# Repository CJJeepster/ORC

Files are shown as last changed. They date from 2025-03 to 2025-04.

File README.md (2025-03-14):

# ORC
WSU Capstone 2025

ORC is a active suspension system for an RC car, in this case RC4WD's Trail finder 2. The design documentation, source code, python code, custom parts, schematics, and PCBs are included in their own folders. 

The source code is intended to be built with Espressif's ESP-ID v5.4.0, which can be a standalone toolchain, or VScode extension. 
The python code is run with python 3.12 using the following libraries: csv, matplotlib, numpy, scipy, and collections. This will take the logged data, calculate some statistics, and plot the repeated runs.
The custom parts were designed in FreeCAD 1.0.0, with both STL files and the original files included. 
The schematics and PCBs were designed in KiCAD 8.0. A seperate "revisions" document details the shortcomings of this design. Fixes are not yet implemented to preserve the current state of the board and save development time.

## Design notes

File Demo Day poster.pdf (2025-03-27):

Corbin Roennebeck
Department of Electrical and Computer Engineering Weber State University

## Introduction

## Project Goals

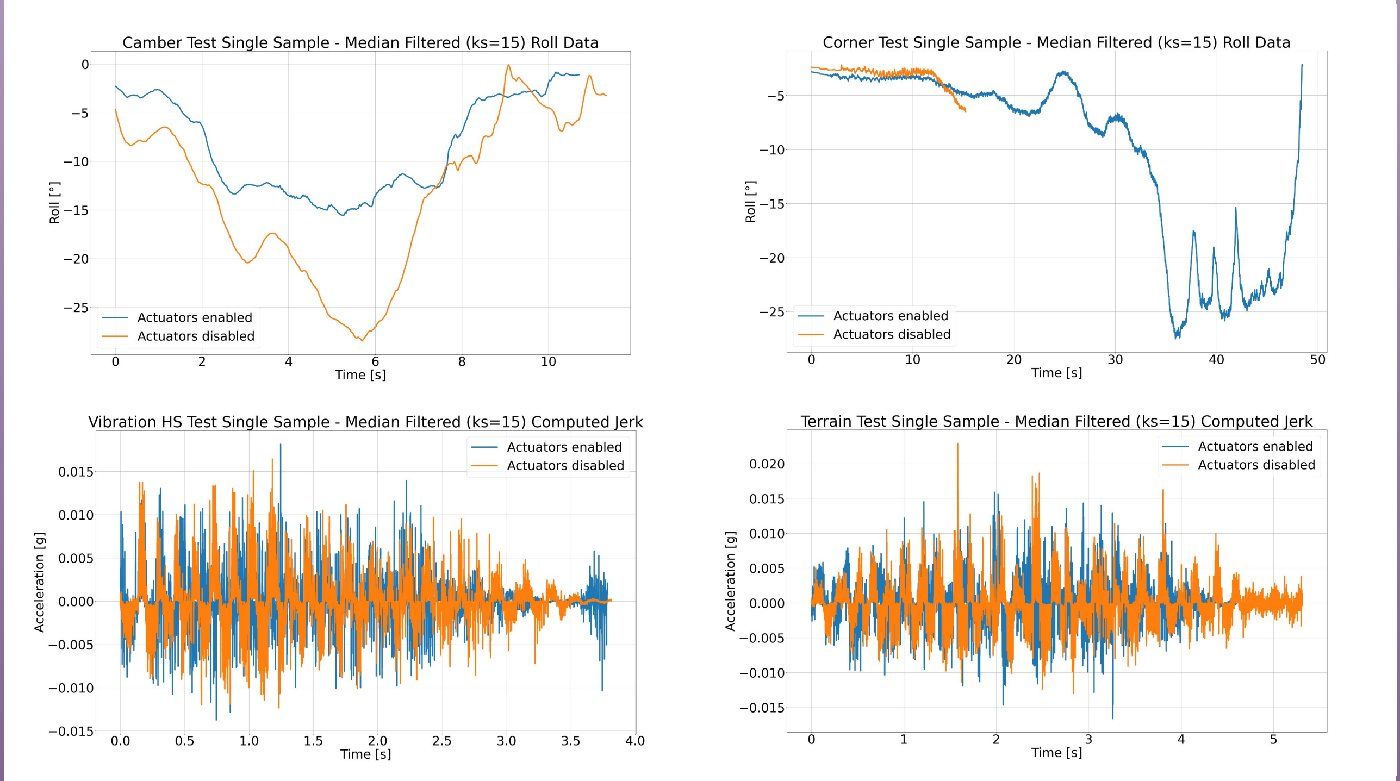
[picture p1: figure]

## Methods

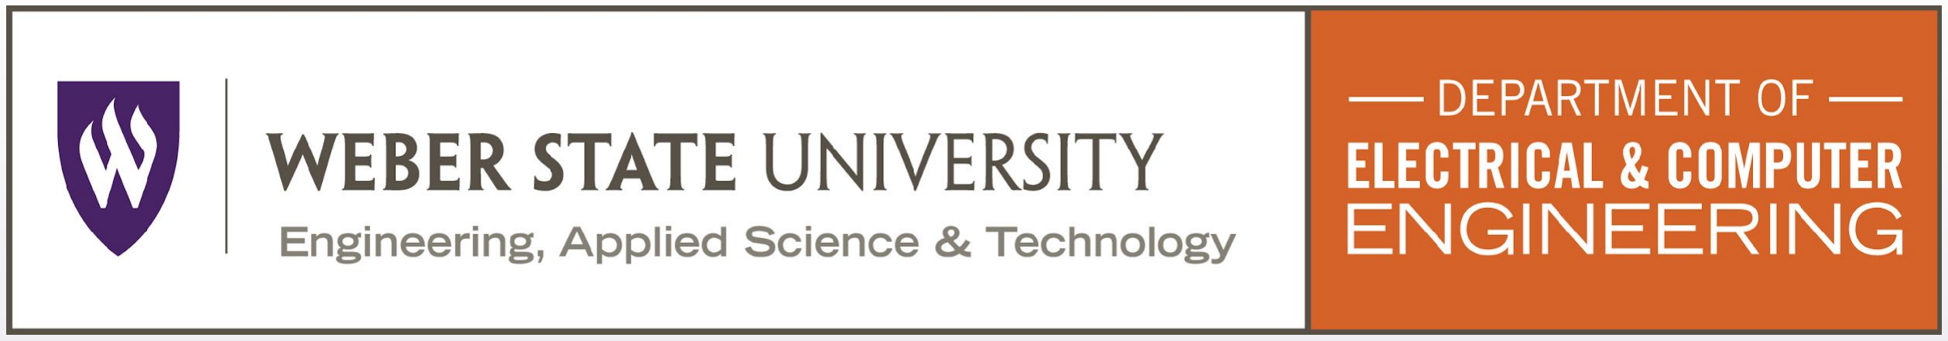
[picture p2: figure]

Figures and Results | Conclusion

## Acknowledgments

## References

The Off-Road Roll Control (ORC) project seeks to provide high performance vehicle suspension at budget build prices. Large off road vehicles, like the modern Jeep Wrangler, are top heavy and prone to rolling over in off-balance situations. This problem is exacerbated by disconnected sway bars, lifted suspensions, roll cages, and body armor.
In extreme cases, a vehicle similar to the one described prior could roll over as a result of a low speed emergency maneuver. To help mitigate handling issues like this and to improve passenger comfort overall, an active suspension system is proposed here.

Similar to [1], PID control of actuators is the primary control methodology. The PID controllers respond to vertical acceleration, pitch, and roll. These are measured by an inertial measurement system (IMU), the data from which is combined and filtered. The output of the 3 PIDs are transformed into 4 actuator movements, present at each corner of the vehicle. The outer loop from [1] is excluded as its effect was minimal and increased complexity significantly. Were development of this platform to continue, better tuning, or automatic tuning, of the PID controllers could reveal more performance. Other control algorithms such as fuzzy logic or the many others suggested in [3] could be tested. Using a voice coil actuator could also prove to improve ride quality further by decreasing response time.

# Off-Road Roll Control

Many thanks are extended to the ECE department faculty, especially Dr. Fon Brown, for their extensive support and excellent guidance.
Special thanks are due to Audrey Roennebeck, without whose support this project would not have been possible.

To implement actuators on a scale prototype, several solutions were explored, but ultimately a gear motor with a lever arm was chosen. This solution allowed the suspension to move freely, without too much damping coming from the motors themselves. These gear motors are mounted to the frame of an 1/10 scale RC rock crawler. Linkages connect the lever arm to the axle on both the driver and passenger side of the vehicles. By varying the magnitude and polarity of the current sent to these motors, a variable force between the axle and frame can be realized.
This variable current comes from the custom motor driver boards, which take a ±2.5V signal from the main board’s DAC and converts it to a ±16V signal used to drive the motors up to about 2A.

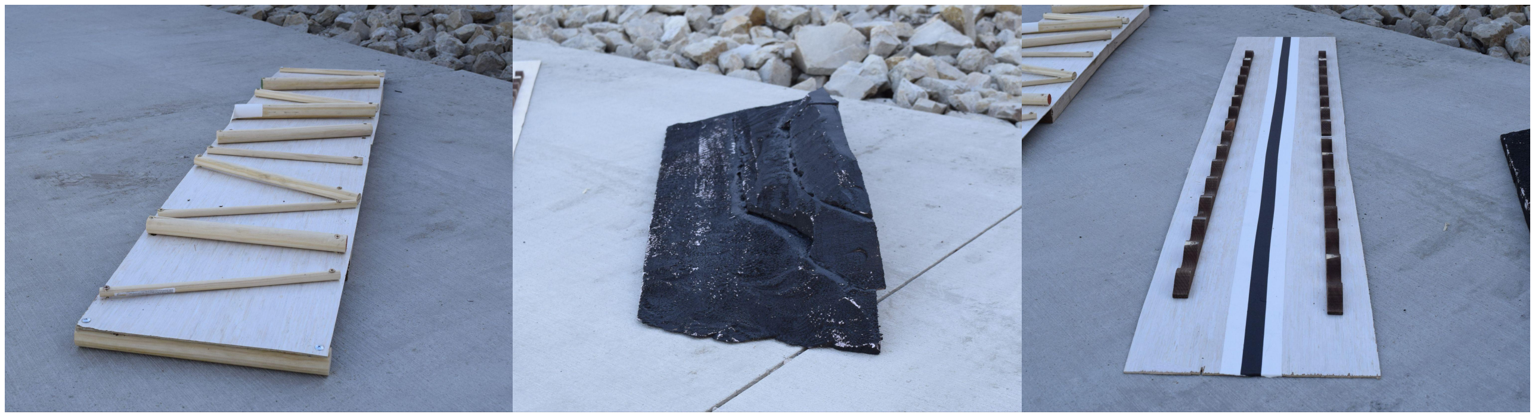
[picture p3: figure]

[1] D. Tan, C. Lu, and X. Zhang, “Dual-loop PID control with PSO algorithm for the active suspension of the electric vehicle driven by in-wheel motor,” Journal of Vibroengineering, vol. 18, no. 6, pp. 3915–3929, Sep. 2016, doi: 10.21595/jve.2016.16689.
[2] J. Sun, J. Cong, W. Zhao, and Y. Zhang, “Quantized Feedback Control of Active Suspension Systems Based on Event Trigger,” Shock and vibration, vol. 2021, pp. 1–15, May 2021, doi: https://doi.org/10.1155/2021/8886069.
[3] Kevin Herubiel Floreán-Aquino, M. Arias-Montiel, J. Linares-Flores, José Gabriel Mendoza-Larios, and
A. Cabrera-Amado, “Modern Semi-Active Control Schemes for a Suspension with MR Actuator for Vibration Attenuation,” Actuators, vol. 10, no. 2, pp. 22–22, Jan. 2021, doi: https://doi.org/10.3390/act10020022.

ORC improves passenger comfort by reducing experienced pitch, roll, and vertical jerk relative to a vehicle with no dampers. A real time system contained to only the equipped vehicle is desired. For practical reasons, a 1/10 scale vehicle platform is demonstrated.

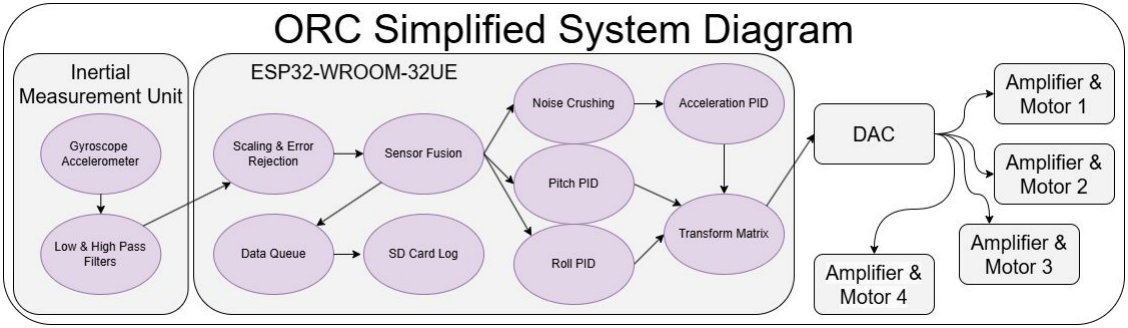
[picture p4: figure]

To examine the effects of the control system on vehicle dynamics, the pitch, roll, and vertical acceleration of the vehicle are recorded. From the vertical acceleration data, the jerk (representing the smoothness of the ride) can be derived. This data is recorded while driving over bumpy terrain, off camber, and through tight corners.
The same terrain (pictured below) is used for testing with actuators enabled, and disabled. Each terrain is driven with a constant speed and minor steering inputs to keep the vehicle on track. Where possible, 20+ test runs were conducted for each actuator status.

One Sided T Test Statistics For Improved (Absolutely Less) RMS, Minimum, and Maximum Values

P-value\Test | Camber (min direction) | Terrain | Vibration High Speed* | Vibration Low Speed | Corner*
Acceleration RMS | 6.27E-20 | 3.84E-03 | 1.06E-06 | 1.10E-09 | 1.00E+00
Pitch RMS | 1.19E-07 | 1.65E-09 | 1.65E-01 | 3.10E-33 | 9.92E-01
Roll RMS | 9.81E-20 | 2.92E-27 | 1.54E-02 | 1.02E-24 | 9.22E-01
Jerk RMS | 1.00E+00 | 1.00E+00 | 4.45E-01 | 1.00E+00 | 9.89E-01
Acceleration MIN | 7.92E-14 | 9.44E-01 | 4.42E-05 | 1.00E+00 | 7.28E-01
Pitch MIN | 6.98E-13 | 1.15E-05 | 1.78E-01 | 4.59E-01 | 9.69E-01
Roll MIN | 2.93E-35 | 4.83E-21 | 3.16E-04 | 5.79E-26 | 9.65E-01
Jerk MIN | 1.00E+00 | 1.00E+00 | 9.96E-01 | 1.00E+00 | 8.33E-01
Acceleration MAX | 9.97E-01 | 4.26E-01 | 1.52E-06 | 1.38E-18 | 9.89E-01
Pitch MAX | 1.00E+00 | 3.26E-16 | 9.15E-03 | 2.53E-27 | 9.83E-01
Roll MAX | 6.18E-01 | 7.81E-34 | 3.91E-04 | 2.40E-12 | 8.60E-01
Jerk MAX | 1.00E+00 | 9.08E-03 | 7.33E-01 | 1.00E+00 | 8.30E-01

*Only tested 5 samples instead of full 20+
(Gray fill not relevant to particular test, included for completeness) | >5% CI | <5% CI

The ORC system’s ability to reduce vehicle roll and jerk is mixed. In almost every case the roll of the vehicle was statistically significantly reduced. In all but one case the experienced jerk was not shown to be significantly less when the actuators were enabled. This is not to say the vehicle performed worse, but the difference between the groups was not large enough to be decisive.
A two sample one sided t-test was used to show statistically significant improvement in ride quality within a 5% confidence interval (CI). The RMS, minimum, and maximum value of each test run was put in one of two data sets (actuators enabled/disabled). This does assume the data follows a normal distribution.
While not part of the initial testing plan, the number of revolutions completed in the corner test was evaluated. This showed significant improvement in cornering ability with a P value of 0.0166, which is well within the 5% CI.
Overall, ORC was successful in improving ride quality, but it is likely that some performance was still left on the table.

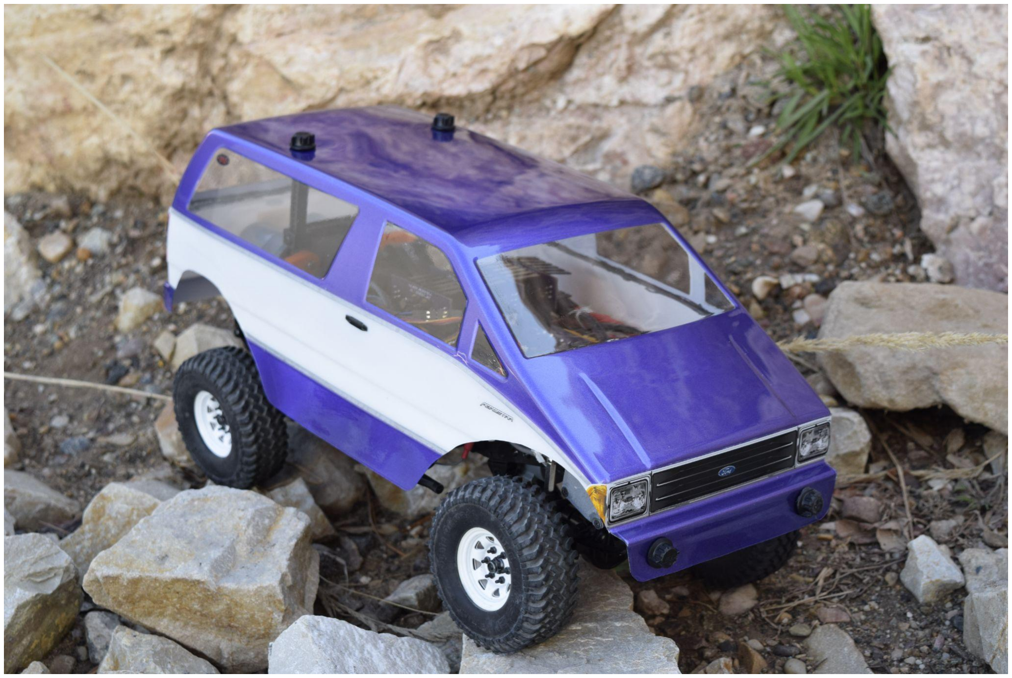
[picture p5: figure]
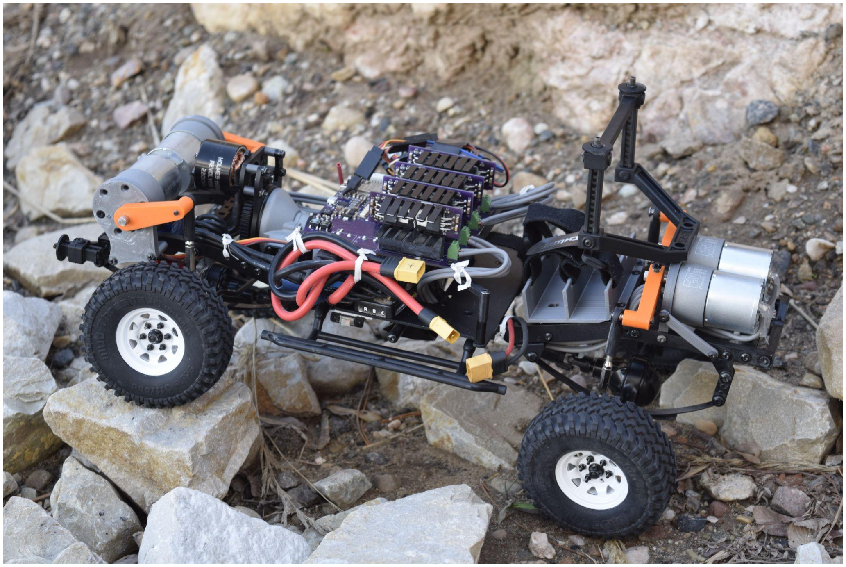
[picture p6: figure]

The collected data was processed with a Python script that applied a median filter to knock out random peak readings, plotted a single run’s data, and performed a one-sided T-test, discussed in the next section. Selected plots are displayed below.

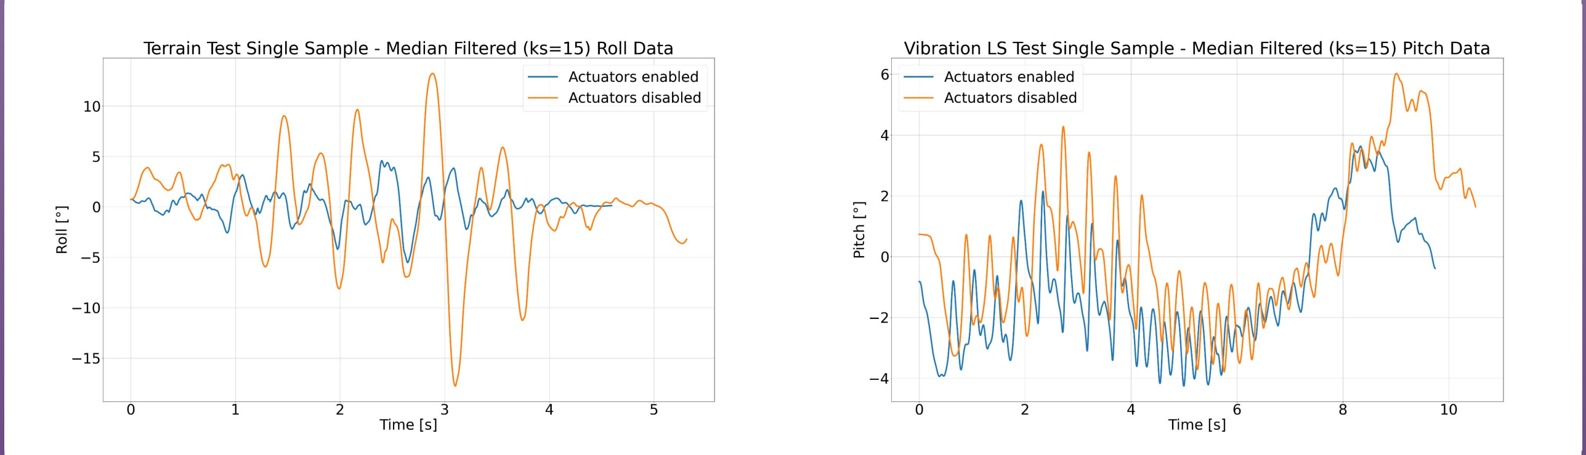
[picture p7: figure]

All of the plots and test results are fairly representative of the actual vehicle dynamics except those from the corner test. This test involved driving at increasing speed with a fixed steering input until the vehicles max speed was reached or the vehicle rolled. The induced centrifugal force confused the sensor fusion algorithm, causing it to misinterpret the direction of gravity and thus the euler angles of the system. To combat this, the number of revolutions completed by the vehicle were counted, where the vehicle with the actuators enabled completed 30.9 rotations on average compared to the actuators disabled completing an average of 5.5.

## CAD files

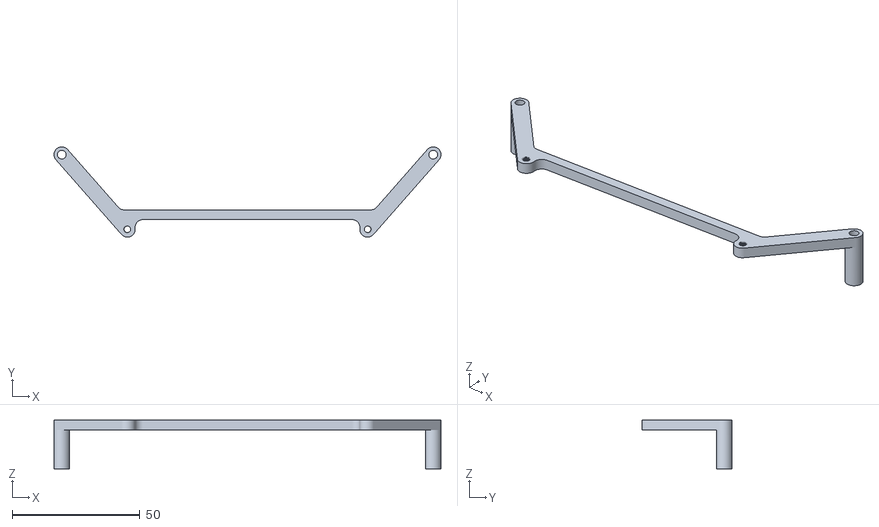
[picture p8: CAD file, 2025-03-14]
3D models/stl/main board mount rear-BodyMirrored.stl
151.4 x 35.3 x 19.0

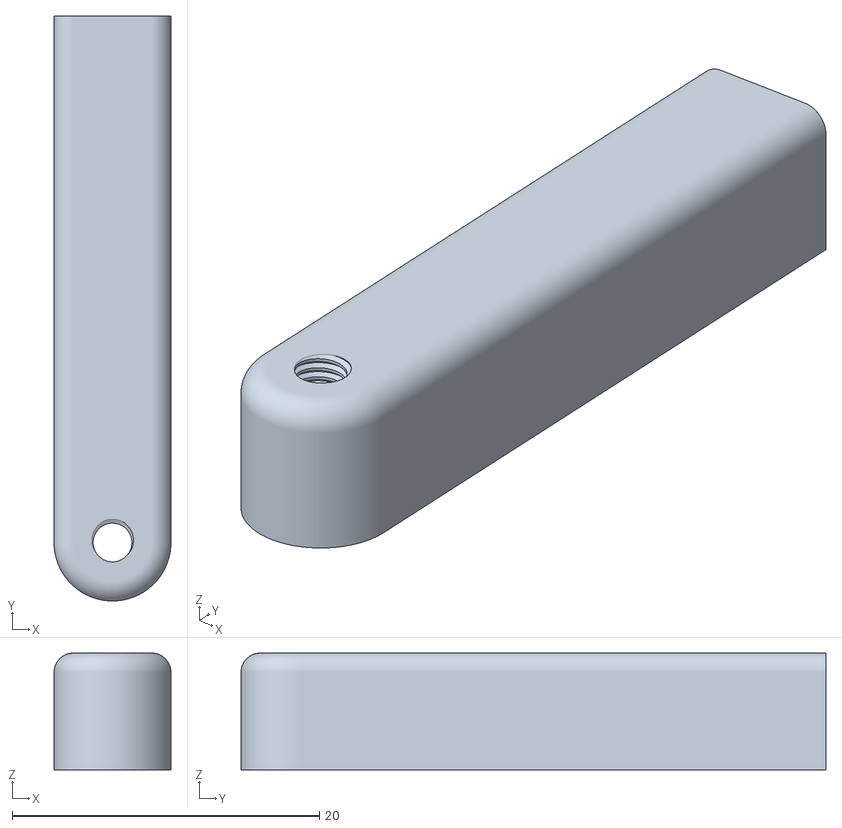
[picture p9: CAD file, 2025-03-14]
3D models/stl/main board mount front-Body.stl
7.62 x 38.1 x 7.62

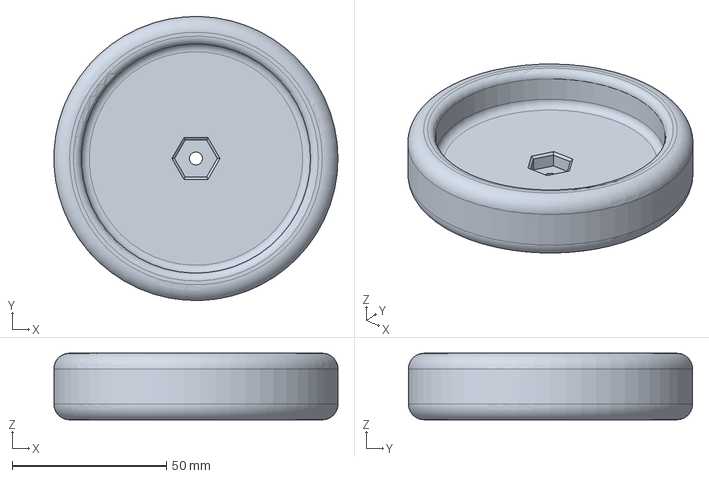
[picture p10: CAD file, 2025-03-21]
3D models/FreeCAD/Tight turn slide wheel.FCStd
92.0 x 92.0 x 21.6 mm

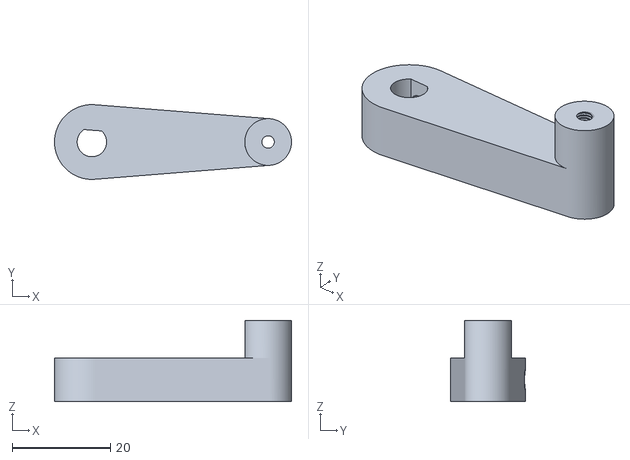
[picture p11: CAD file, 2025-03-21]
3D models/stl/Arm-Body.stl
48.3 x 15.2 x 16.5

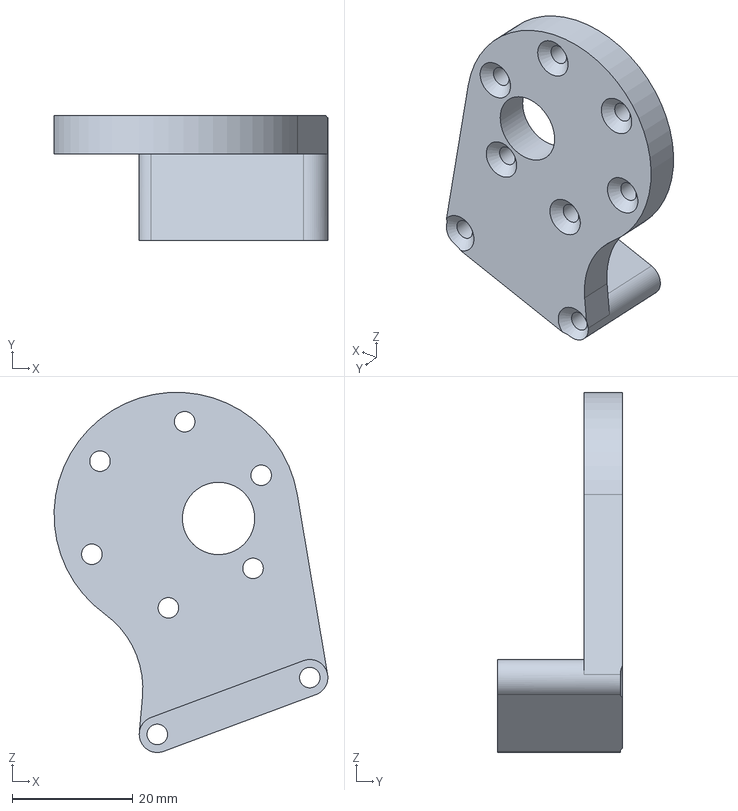
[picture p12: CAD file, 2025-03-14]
3D models/FreeCAD/front bracket v2.FCStd
45.4 x 20.7 x 59.7 mm

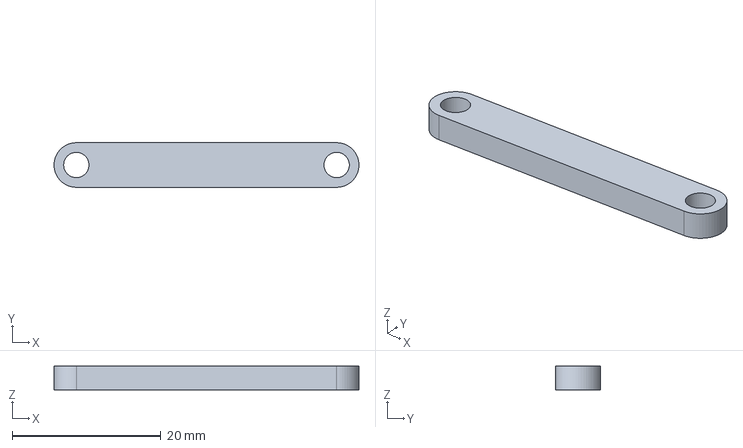
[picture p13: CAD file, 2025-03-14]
3D models/FreeCAD/front bracket support brace.FCStd
41.0 x 6.00 x 3.17 mm

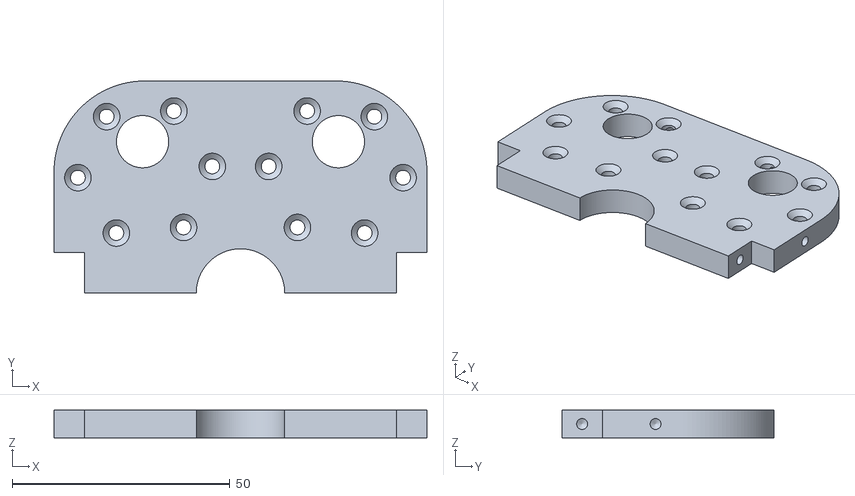
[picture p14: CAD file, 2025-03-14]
3D models/stl/rear bracket-Body.stl
85.7 x 48.8 x 6.35

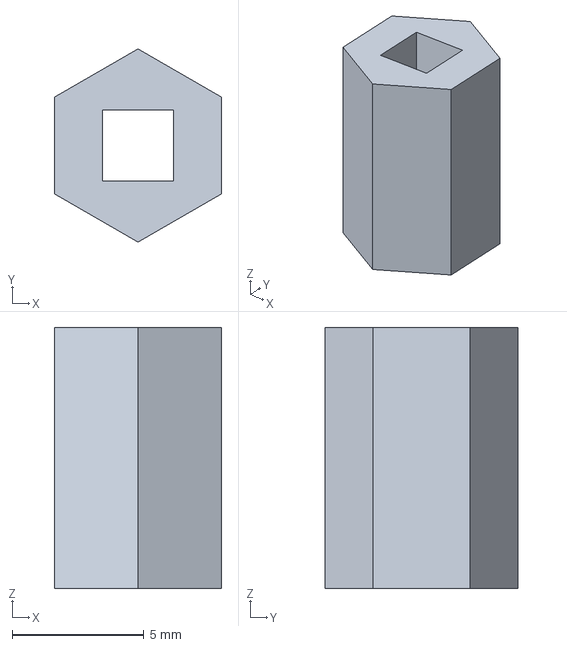
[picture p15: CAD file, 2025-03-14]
3D models/FreeCAD/M3 Tap adapter.FCStd
6.35 x 7.33 x 9.91 mm

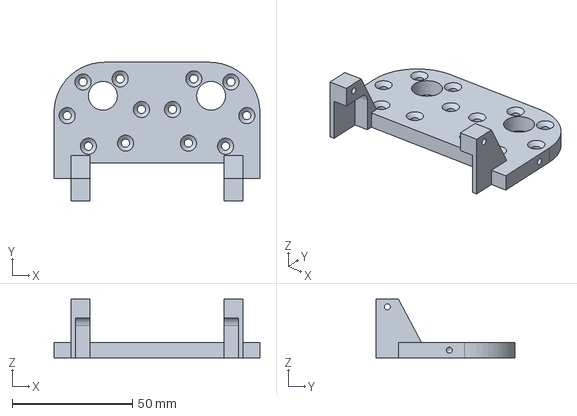
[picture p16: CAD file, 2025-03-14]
3D models/FreeCAD/front bracket.FCStd
85.7 x 57.6 x 24.3 mm

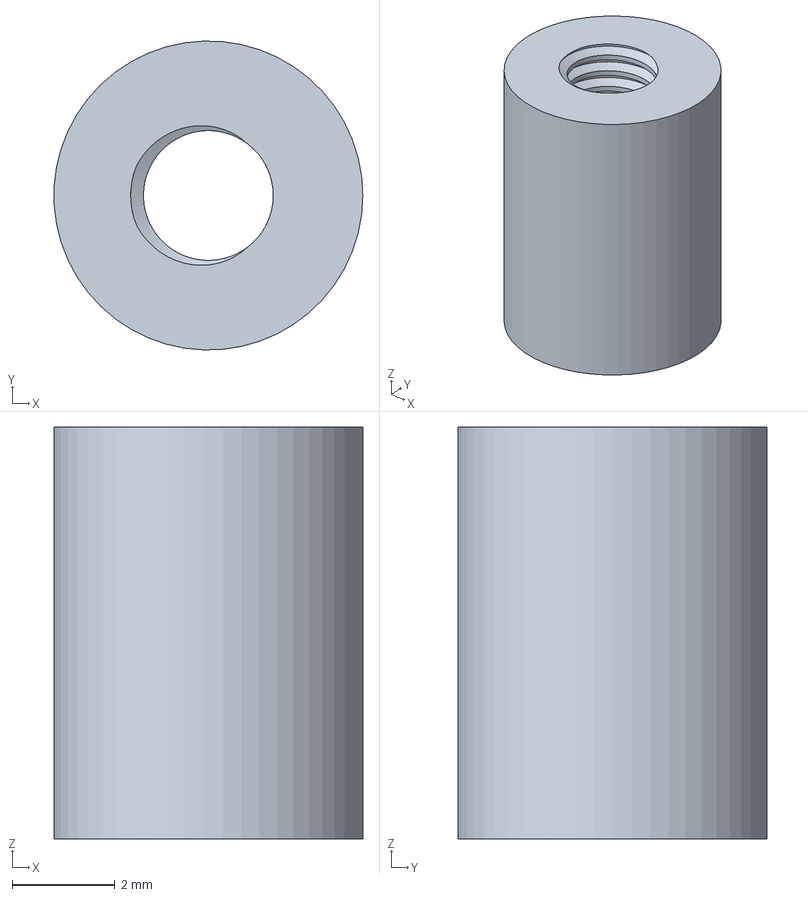
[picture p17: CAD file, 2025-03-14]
3D models/FreeCAD/8mm M3 spacer.FCStd
5.99 x 6.00 x 8.00 mm

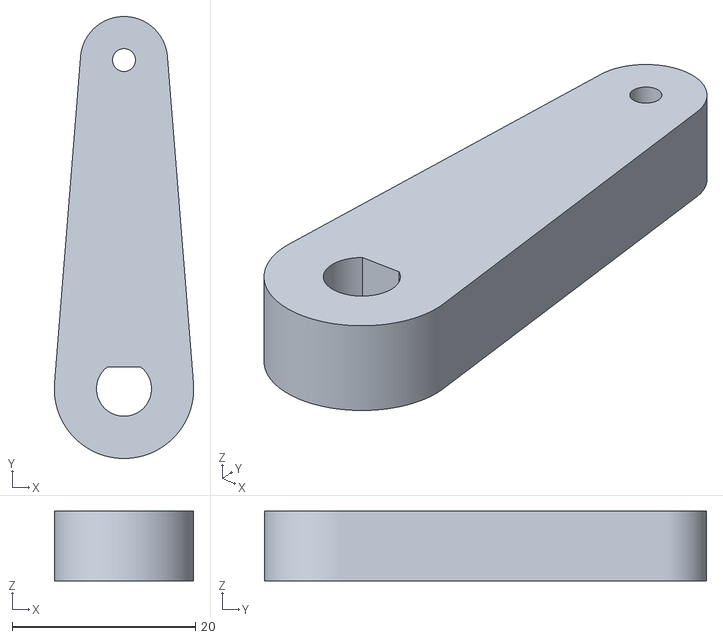
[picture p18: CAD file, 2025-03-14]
3D models/stl/lever Arm.stl
15.2 x 48.3 x 7.62

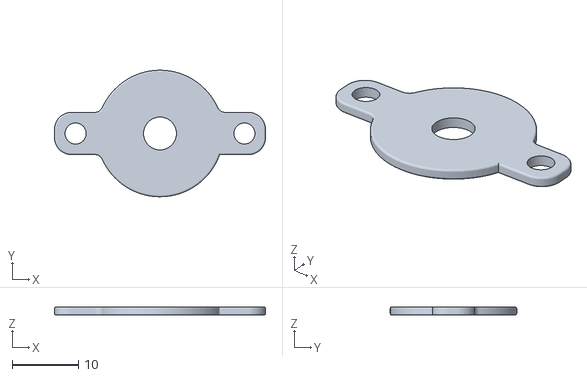
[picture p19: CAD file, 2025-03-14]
3D models/stl/End+Cap.stl
31.8 x 19.0 x 1.27

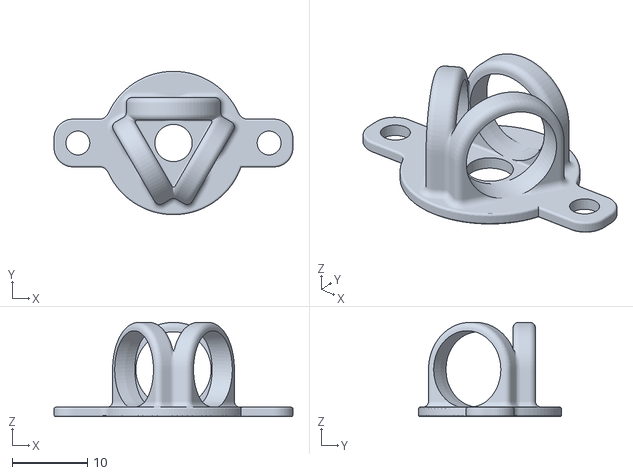
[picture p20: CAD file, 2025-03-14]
3D models/stl/Magnet+Cap.stl
31.8 x 19.0 x 12.5

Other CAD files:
3D models/FreeCAD/main board mount front.FCStd
3D models/FreeCAD/main board mount rear.FCStd
3D models/FreeCAD/Arm.FCStd
3D models/stl/Tight turn slide wheel-Body.stl
3D models/stl/front bracket support brace-Body.stl
3D models/FreeCAD/Motot.FCStd
3D models/FreeCAD/Rear Battery Mounts.FCStd
3D models/FreeCAD/Sensor Mount Back.FCStd
3D models/FreeCAD/Sensor Mount Front.FCStd
3D models/FreeCAD/rear bracket support brace.FCStd
3D models/FreeCAD/rear bracket.FCStd
3D models/stl/8mm M3 spacer-Body.stl
3D models/stl/8mm M3 spacer-BodySketch001.stl
3D models/stl/Arm-BodyHole.stl
3D models/stl/Arm.stl
3D models/stl/M3 Tap adapter-Body.stl
3D models/stl/Rear Battery Mounts-Body.stl
3D models/stl/Sensor Mount Back-Body.stl
3D models/stl/Sensor Mount Front-Body.stl
3D models/stl/Trail_Finder_2_Chassis.stl
3D models/stl/VC+spool.stl
3D models/stl/front bracket v2-Body.stl
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

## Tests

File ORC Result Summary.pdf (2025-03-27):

## One Sided T Test Statistics For Improved (Absolutely Less) RMS, Minimum, and

Maximum Values | Average RMS, Minimum, and Maximum values. Actuators Enabled | Actuators Disabled
P-value\Test | Camber (min direction) | Terrain | Vibration High Speed* | Vibration Low Speed | Corner* | P-value\Test | Camber (min direction) | Terrain | Vibration High Speed* | Vibration Low Speed | Corner* | Corner Completed Revolutions*
6.27E-20 | 3.84E-03 | 1.06E-06 | 1.10E-09 | 1.00E+00 | 1.81E-02 | 5.26E-02 | 1.99E-01 | 2.06E-01 | 1.01E-01 | 1.49E-01 | 6.62E-02 | 7.58E-02 | 1.39E-01 2.96E-02 | Average
1.19E-07 | 1.65E-09 | 1.65E-01 | 3.10E-33 | 9.92E-01 | 4.88E+00 | 5.37E+00 | 4.42E+00 | 5.84E+00 | 2.50E+00 | 2.66E+00 | 2.10E+00 | 2.50E+00 | 9.56E+00 2.65E+00 | 3.09E+01 | 5.50E+00
9.81E-20 | 2.92E-27 | 1.54E-02 | 1.02E-24 | 9.22E-01 | 9.76E+00 | 1.54E+01 | 1.59E+00 | 5.13E+00 | 1.08E+00 | 1.31E+00 | 8.13E-01 | 2.00E+00 | 1.24E+01 7.59E+00
1.00E+00 | 1.00E+00 | 4.45E-01 | 1.00E+00 | 9.89E-01 | 3.40E-04 | 2.80E-04 | 2.83E-03 | 2.61E-03 | 2.45E-03 | 2.46E-03 | 1.01E-03 | 8.70E-03 | 3.02E-03 1.28E-03
7.92E-14 | 9.44E-01 | 4.42E-05 | 1.00E+00 | 7.28E-01 | -7.88E-02 | -1.25E-01 | -5.73E-01 | -5.46E-01 | -3.25E-01 | -4.64E-01 | -1.88E-01 | -1.67E-01 | -2.49E-01 -1.36E-01 | Minimum
6.98E-13 | 1.15E-05 | 1.78E-01 | 4.59E-01 | 9.69E-01 | -8.44E+00 | -1.02E+01 | -7.12E+00 | -9.66E+00 | -1.94E+00 | -2.68E+00 | -3.95E+00 | -3.96E+00 | -2.54E+01 -1.00E+01 | 1.53E+01 | 4.75E+00
2.93E-35 | 4.83E-21 | 3.16E-04 | 5.79E-26 | 9.65E-01 | -1.57E+01 | -2.72E+01 | -5.96E+00 | -1.73E+01 | -2.31E+00 | -4.11E+00 | -2.85E+00 | -5.83E+00 | -3.44E+01 -1.71E+01
1.00E+00 | 1.00E+00 | 9.96E-01 | 1.00E+00 | 8.33E-01 | -3.67E-03 | -2.60E-03 | -1.55E-02 | -1.39E-02 | -1.55E-02 | -1.26E-02 | -7.41E-03 | -6.31E-03 | -1.77E-01 -1.62E-02
9.97E-01 | 4.26E-01 | 1.52E-06 | 1.38E-18 | 9.89E-01 | 8.98E-02 | 7.31E-02 | 7.71E-01 | 7.74E-01 | 3.17E-01 | 4.70E-01 | 2.53E-01 | 3.26E-01 | 5.23E-01 1.39E-01 | Maximum
1.00E+00 | 3.26E-16 | 9.15E-03 | 2.53E-27 | 9.83E-01 | 1.03E+01 | 6.14E+00 | 9.79E+00 | 1.28E+01 | 5.59E+00 | 6.25E+00 | 3.75E+00 | 6.03E+00 | 2.72E+01 8.10E+00 | 5.50E+01 | 6.00E+00
6.18E-01 | 7.81E-34 | 3.91E-04 | 2.40E-12 | 8.60E-01 | -4.99E-01 | -6.40E-01 | 4.19E+00 | 1.36E+01 | 3.39E-01 | 1.93E+00 | 1.89E+00 | 4.25E+00 | 1.02E+01 3.26E+00
1.00E+00 | 9.08E-03 | 7.33E-01 | 1.00E+00 | 8.30E-01 | 5.23E-03 | 2.90E-03 | 2.05E-02 | 2.33E-02 | 1.72E-02 | 1.67E-02 | 1.02E-02 | 7.72E-03 | 1.78E+00 1.36E-02
*Only tested 5 samples instead of full 20+
(Gray fill cells not relevant to particular test, included for completeness) | >5% CI | <5% CI
Acceleration RMS | | Acceleration RMS
Pitch RMS | Pitch RMS Roll RMS | Roll RMS
Jerk RMS | Jerk RMS Acceleration MIN | Acceleration MIN
Pitch MIN | | Pitch MIN
Roll MIN | | Roll MIN
Jerk MIN | | Jerk MIN
Acceleration MAX | | Acceleration MAX
Pitch MAX | Pitch MAX Roll MAX | Roll MAX
Jerk MAX | | Jerk MAX
*Only tested 5 samples instead of full 20+ | CC t-test statistic: | 0.01659042943

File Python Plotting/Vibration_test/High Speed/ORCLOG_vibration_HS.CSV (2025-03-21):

Log #: 2690
Actuators enabled
Interval:0.000282
Acceleration | Pitch | Roll
-0.0431 | -1.8325 | -1.0771
-0.0472 | -1.8378 | -1.0734
-0.0482 | -1.8427 | -1.0701
-0.0450 | -1.8474 | -1.0674
-0.0406 | -1.8519 | -1.0651
-0.0356 | -1.8563 | -1.0633
-0.0316 | -1.8604 | -1.0618
-0.0296 | -1.8646 | -1.0602
-0.0278 | -1.8690 | -1.0584
-0.0295 | -1.8732 | -1.0562
-0.0343 | -1.8770 | -1.0537
-0.0370 | -1.8806 | -1.0510
-0.0377 | -1.8837 | -1.0485
-0.0404 | -1.8866 | -1.0462
-0.0439 | -1.8896 | -1.0443
-0.0457 | -1.8925 | -1.0421
-0.0472 | -1.8951 | -1.0397
-0.0500 | -1.8975 | -1.0369
-0.0544 | -1.8999 | -1.0340
-0.0599 | -1.9020 | -1.0312
-0.0648 | -1.9039 | -1.0282
-0.0695 | -1.9061 | -1.0250
-0.0775 | -1.9083 | -1.0215
-0.0865 | -1.9104 | -1.0179
-0.0940 | -1.9119 | -1.0145
-0.0972 | -1.9130 | -1.0111
-0.1003 | -1.9136 | -1.0078
-0.1061 | -1.9140 | -1.0043
-0.1086 | -1.9143 | -1.0003
-0.1097 | -1.9143 | -0.9959
-0.1132 | -1.9142 | -0.9913
-0.1185 | -1.9140 | -0.9865
-0.1238 | -1.9136 | -0.9814
-0.1298 | -1.9126 | -0.9761
-0.1358 | -1.9111 | -0.9706
-0.1387 | -1.9092 | -0.9650
-0.1399 | -1.9072 | -0.9593
-0.1407 | -1.9050 | -0.9535
-0.1413 | -1.9027 | -0.9478
-0.1404 | -1.9004 | -0.9421
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

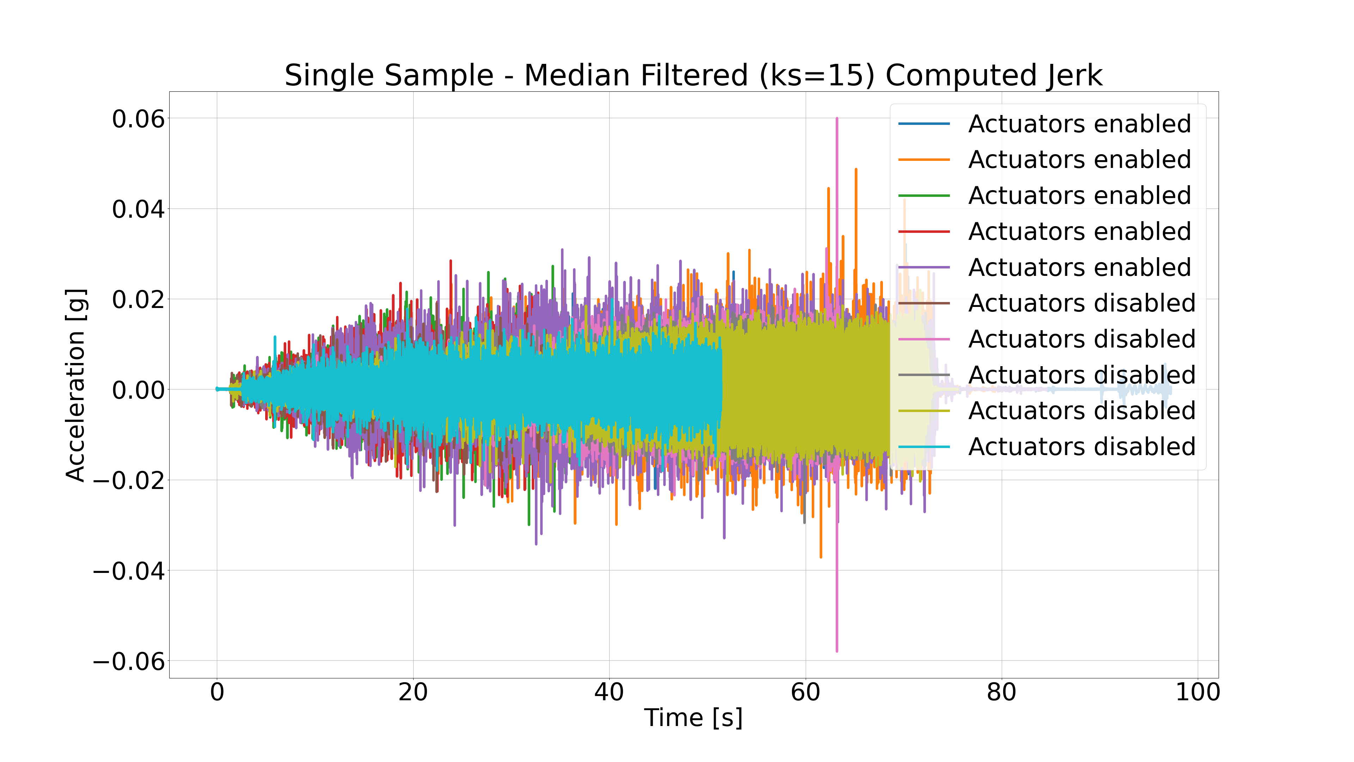
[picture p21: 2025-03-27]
Python Plotting/Corner_test/Corner_1st_try/jerk_corner.png

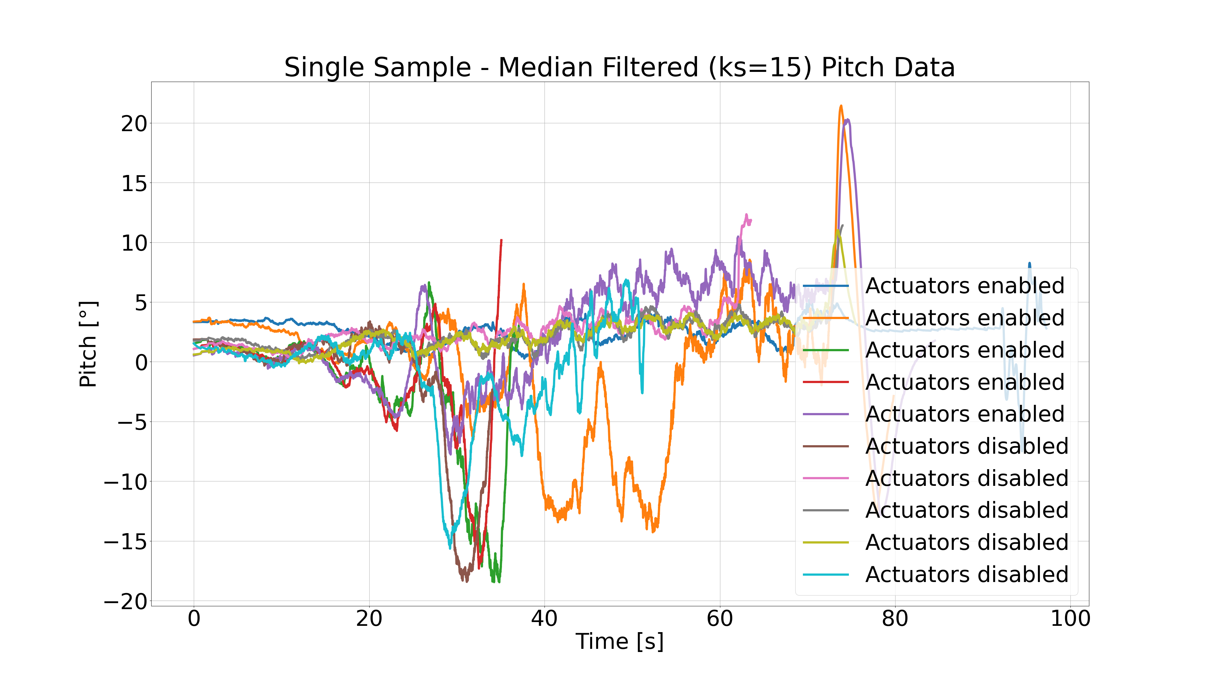
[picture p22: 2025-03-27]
Python Plotting/Corner_test/Corner_1st_try/pitch_corner.png

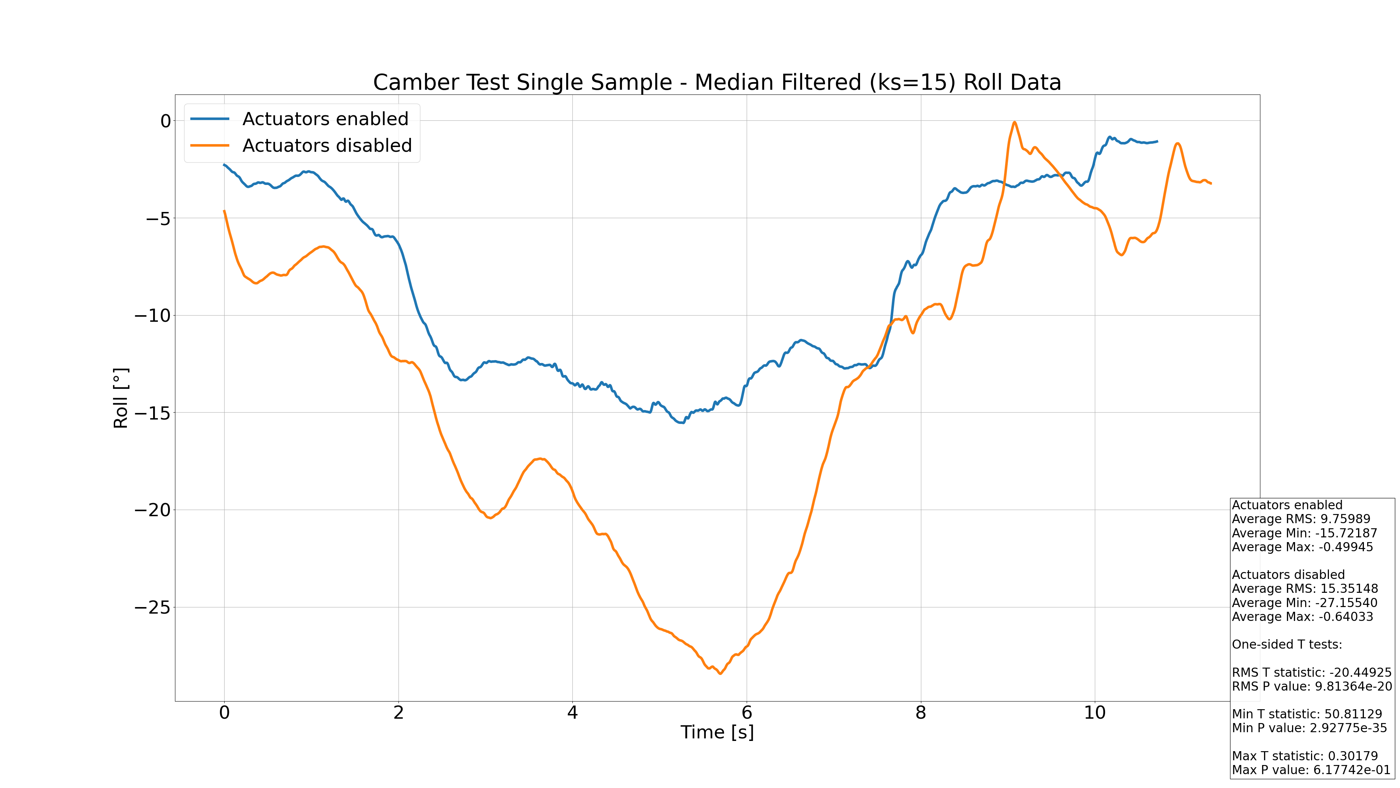
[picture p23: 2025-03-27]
Python Plotting/Camber_test/roll_camber_stats.png

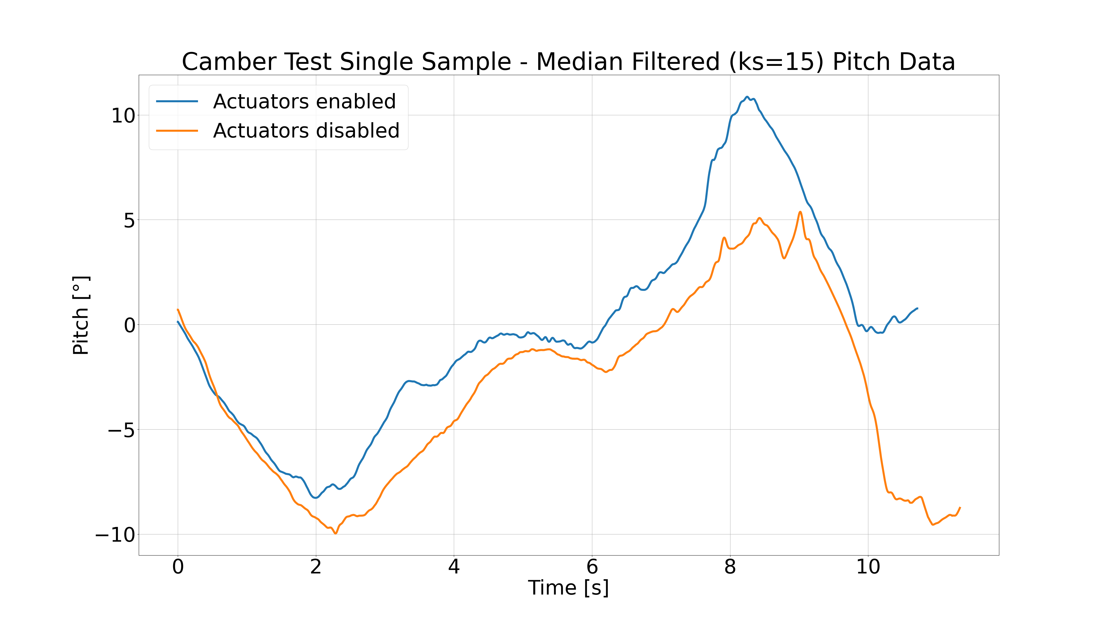
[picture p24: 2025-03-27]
Python Plotting/Camber_test/pitch_camber.png

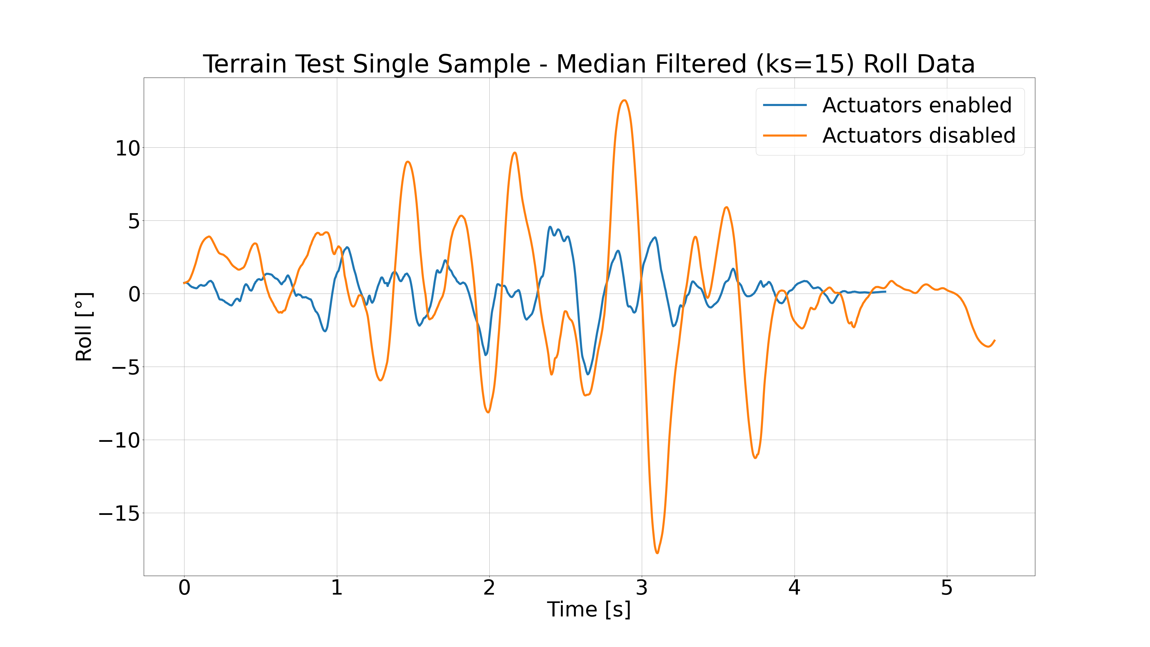
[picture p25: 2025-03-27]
Python Plotting/Terrain_test/roll_terrain.png

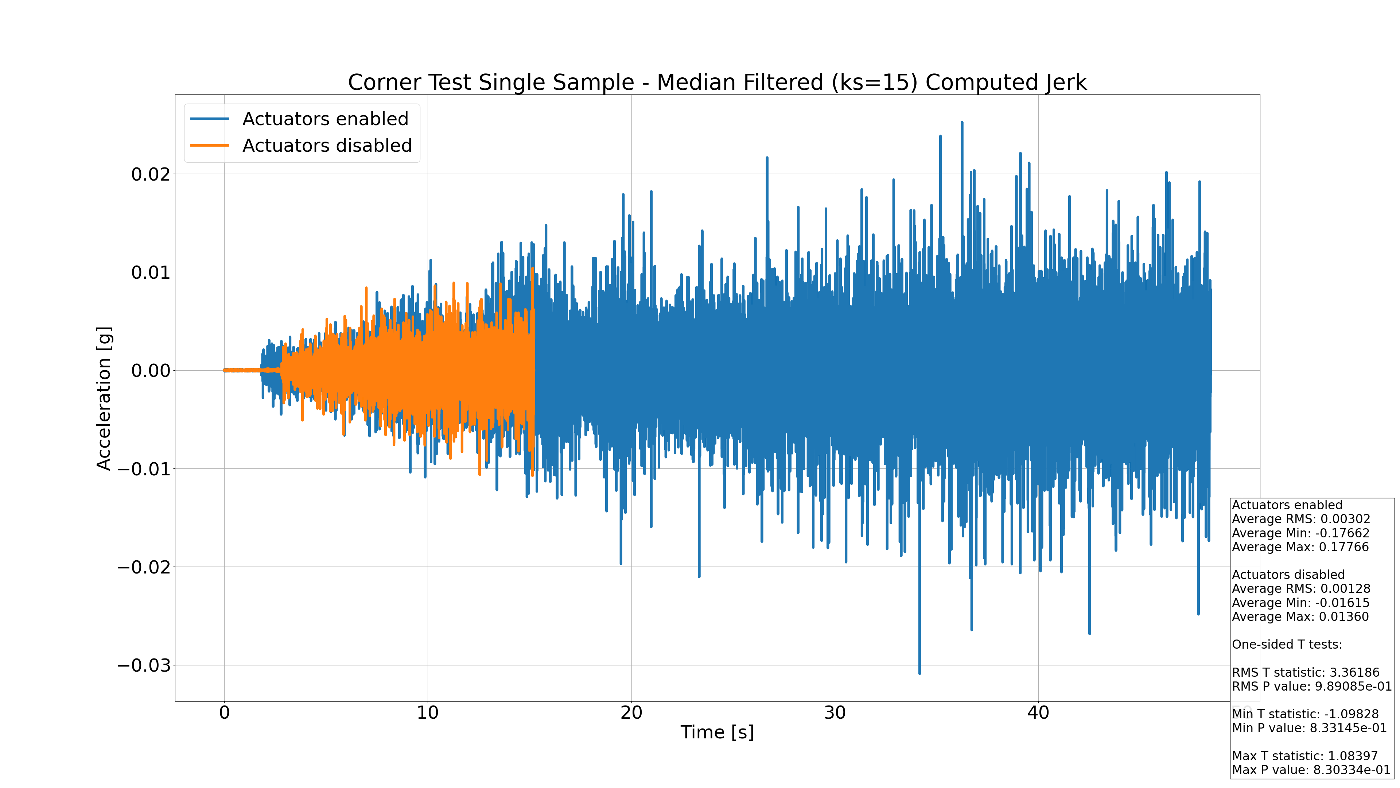
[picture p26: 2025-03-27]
Python Plotting/Corner_test/jerk_Corner_stats.png

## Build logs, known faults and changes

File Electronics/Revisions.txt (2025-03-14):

Revisions Needed:
------------------------------------------------

Main board:
*RX/TX from USB-UART bridge connected to RX/TX on ESP32 respectively, should be connected to TX/RX on ESP32 respectively.
*SDO from ESP32 connected to SDO on DAC. Should be connected to SDI on DAC.
*LED connected to IMU Interupt 1 not needed.
*C11 & R14 Designators need position swapped.
*XT60 battery connectors wrong polarity. Can be installed on bottom of board for temporary relief.
*Recommend PTC fuses on motor outputs for current limiting over time. Protects motor from being burned out. 
*Terminals used for motor outputs rather small. Recommend larger terminal or connector, perhaps XT30
*Excessive audible ringing heard during USB transfers. Needs investigation.
*With button, switch, and LED functions now defined, silkscreen labels are in order.
*Battery voltage cutoff circutry would be very nice to have.
*Fan Header(s) for cooling motor amplifiers would be nice to have.

Motor Amplifier:
*Feedback resistors not matched well to avalible values. Recommend calibration potentiometer to alieviate software calibration necessity.

Other:
*Custom Board for IMU could reduce size and improve wiring connection.
*If pursuing commercial board, smaller components and double sided board would be appropriate. Perhaps integrated amplifiers, rather than daughter cards.
*USB-C would be welcome modernization

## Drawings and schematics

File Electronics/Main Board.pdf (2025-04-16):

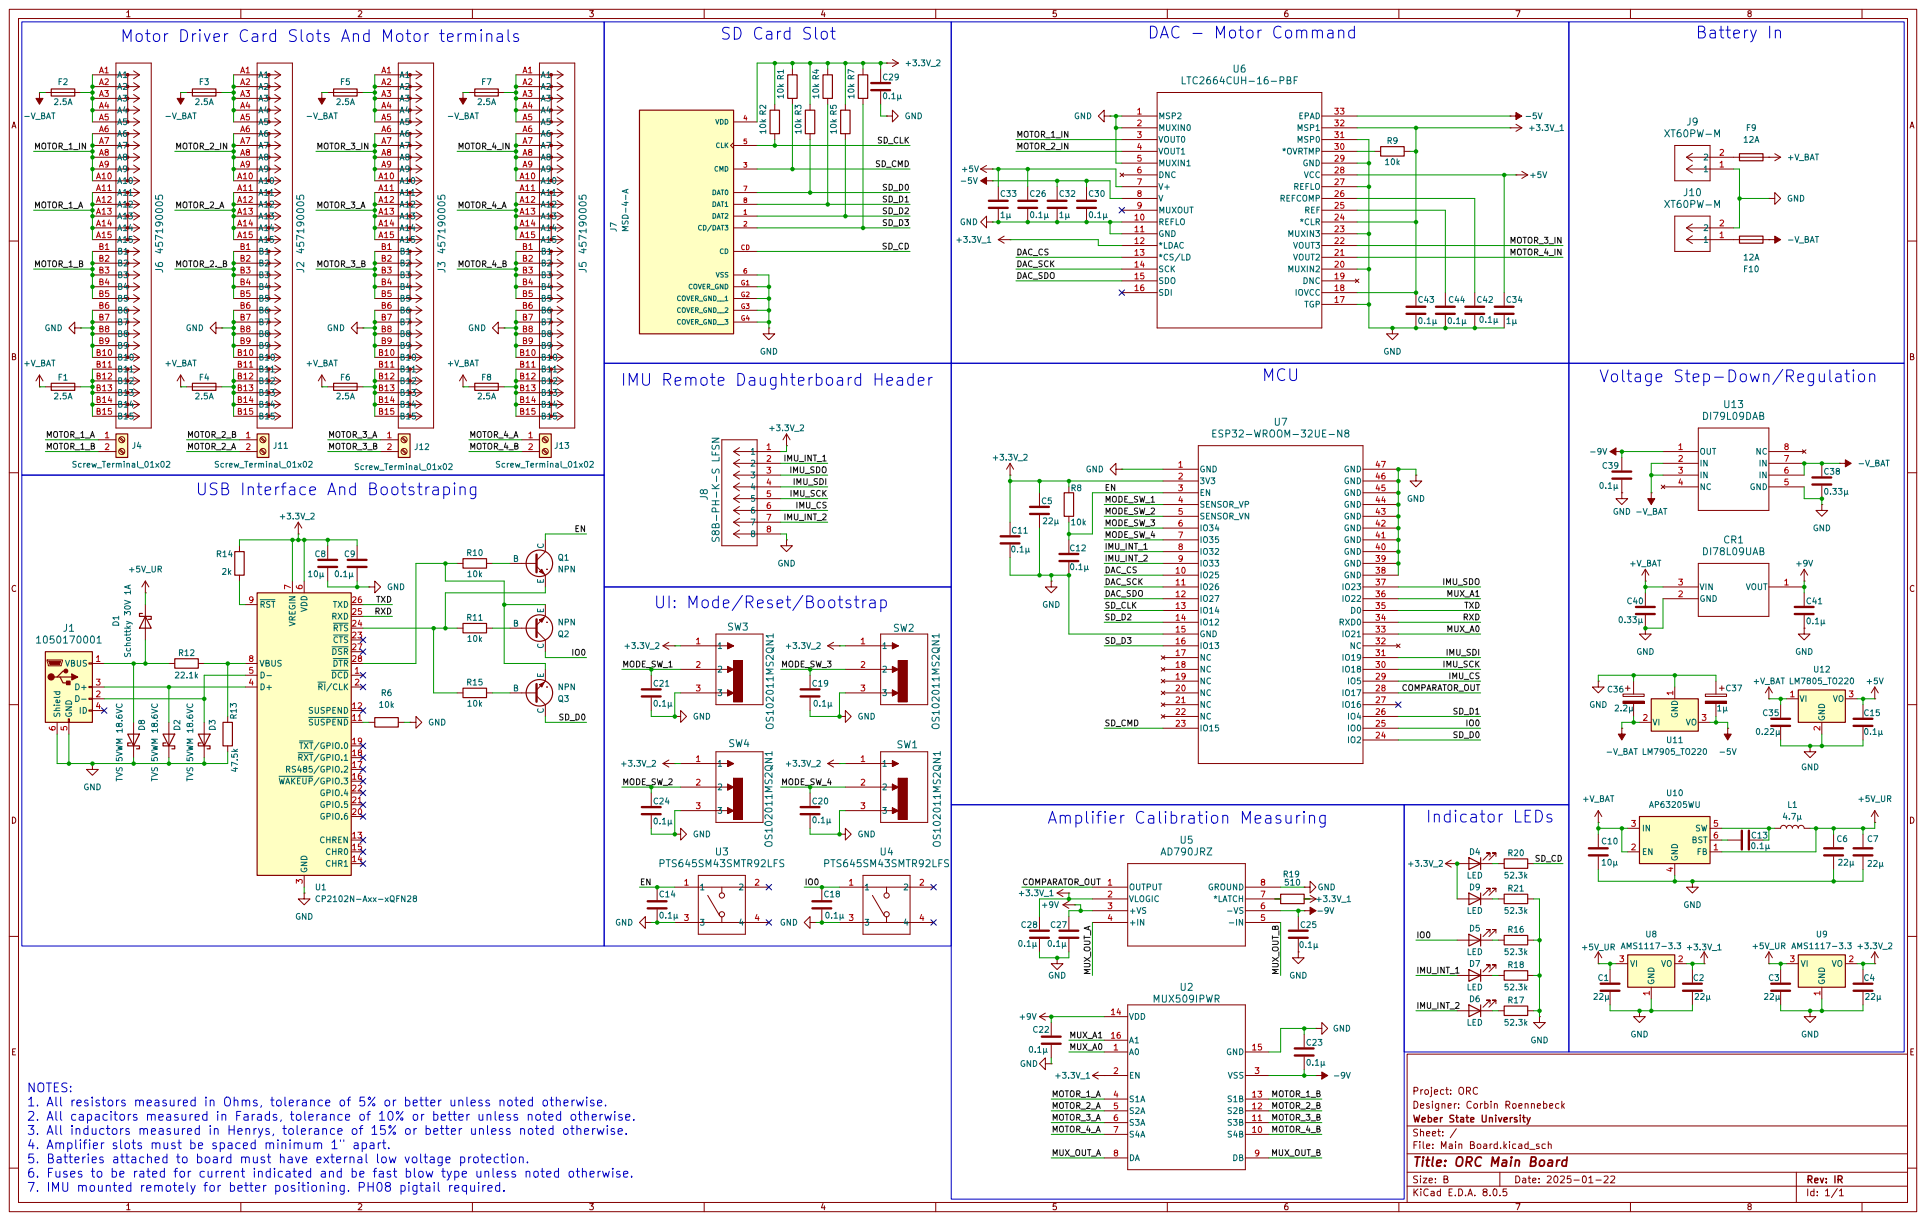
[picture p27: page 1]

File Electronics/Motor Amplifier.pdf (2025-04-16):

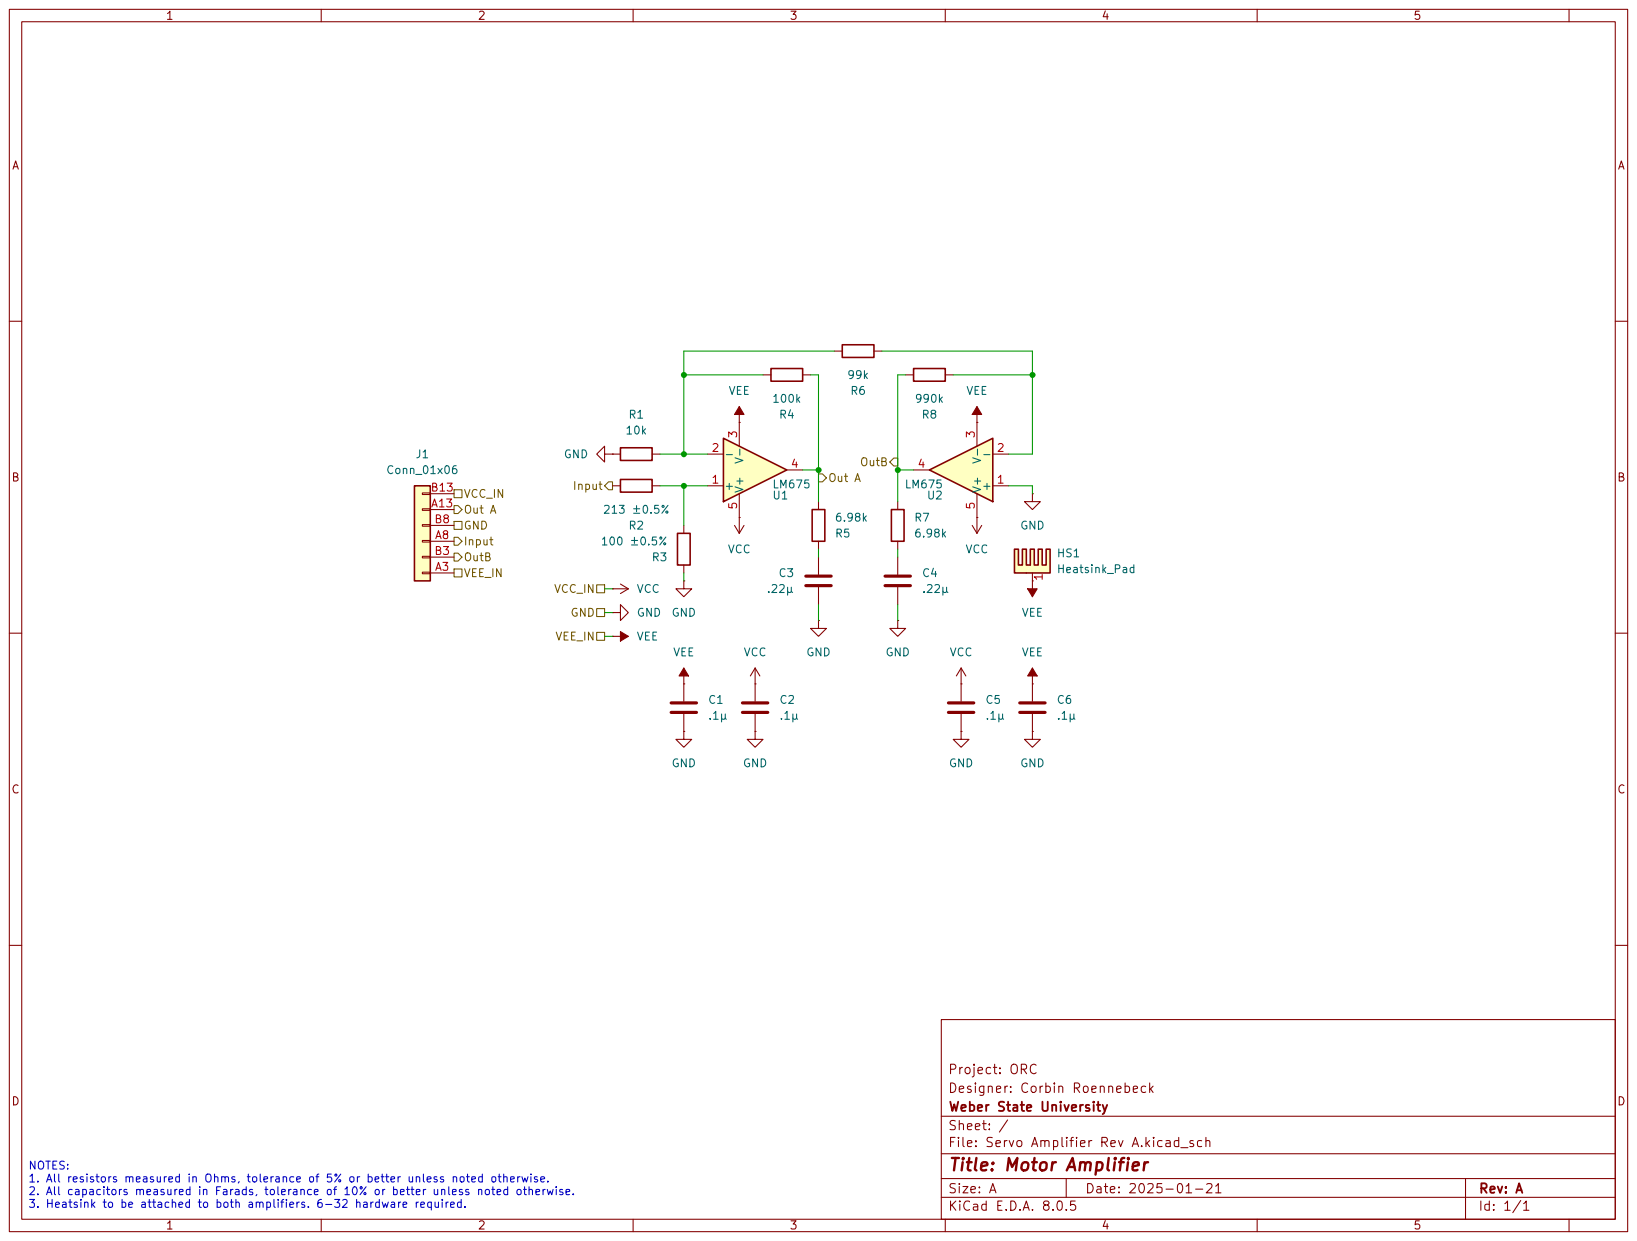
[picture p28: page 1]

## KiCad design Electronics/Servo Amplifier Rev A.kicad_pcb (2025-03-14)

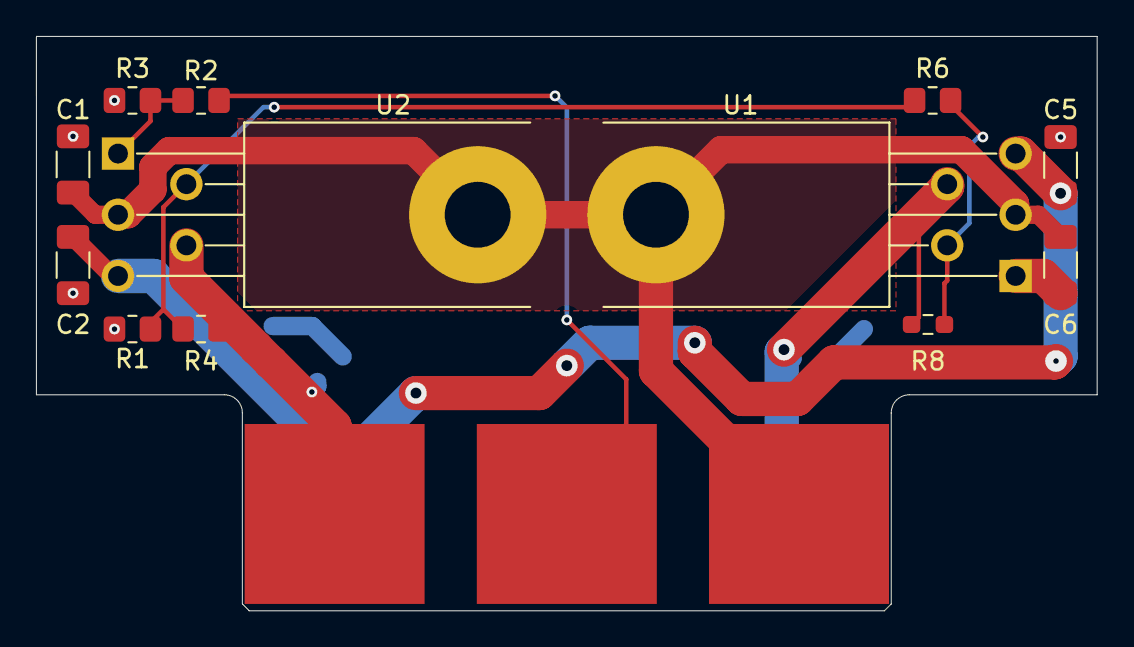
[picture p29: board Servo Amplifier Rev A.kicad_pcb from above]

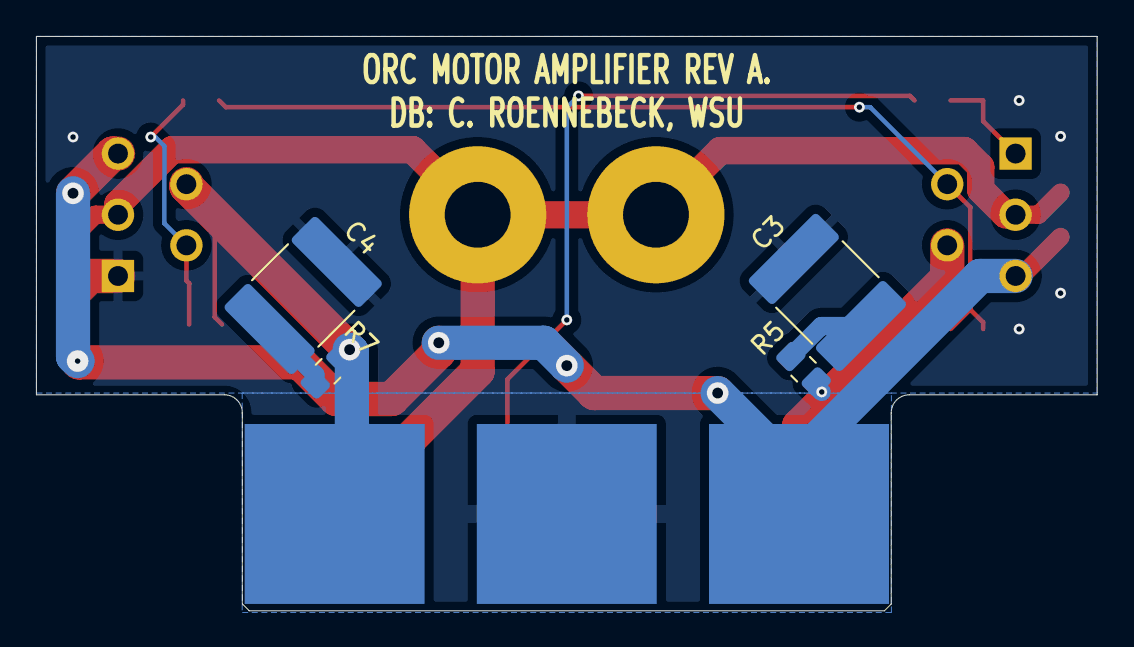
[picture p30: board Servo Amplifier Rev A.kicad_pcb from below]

Board: 2 copper layers, 58.9 x 31.9 mm, 17 parts (4 on the bottom side), 11 nets.

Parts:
C1, C2, C5, C6: .1µ; C_1206_3216Metric_Pad1.33x1.80mm_HandSolder
C3, C4: .22µ; C_2220_5750Metric_Pad1.97x5.40mm_HandSolder
J1: Conn_01x06; MOLEX-45719-0005_PCB_EDGE
R1: 10k; R_0805_2012Metric_Pad1.20x1.40mm_HandSolder
R2: 213 ±0.5%; R_0805_2012Metric_Pad1.20x1.40mm_HandSolder
R3: 100 ±0.5%; R_0805_2012Metric_Pad1.20x1.40mm_HandSolder
R4: 100k; R_0805_2012Metric_Pad1.20x1.40mm_HandSolder
R5, R7: 6.98k; R_0805_2012Metric_Pad1.20x1.40mm_HandSolder
R6: 99k; R_0805_2012Metric_Pad1.20x1.40mm_HandSolder
R8: 990k; R_0603_1608Metric_Pad0.98x0.95mm_HandSolder
U1, U2: LM675; TO-220-5_P3.4x3.8mm_StaggerOdd_Lead7.13mm_TabDown_504222B_HS

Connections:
/Input: J1.A8 (Pin_3), R2.2
/Out A: J1.A13 (Pin_5), R4.2, R5.1, U1.4
/OutB: J1.B3 (Pin_2), R7.1, R8.2, U2.4
GND: C1.2, C2.2, C3.2, C4.2, C5.2, C6.2, J1.B8 (Pin_4), R1.2, R3.2, U2.1 (+)
unnamed: C3.1, R5.2
unnamed: C4.1, R7.2
unnamed: R2.1, R3.1, U1.1 (+)
unnamed: R1.1, R4.1, R6.2, U1.2 (-)
unnamed: R6.1, R8.1, U2.2 (-)
VCC: C2.1, C5.1, J1.B13 (Pin_6), U1.5 (V+), U2.5 (V+)
VEE: C1.1, C6.1, J1.A3 (Pin_1), U1.3 (V-), U2.3 (V-)

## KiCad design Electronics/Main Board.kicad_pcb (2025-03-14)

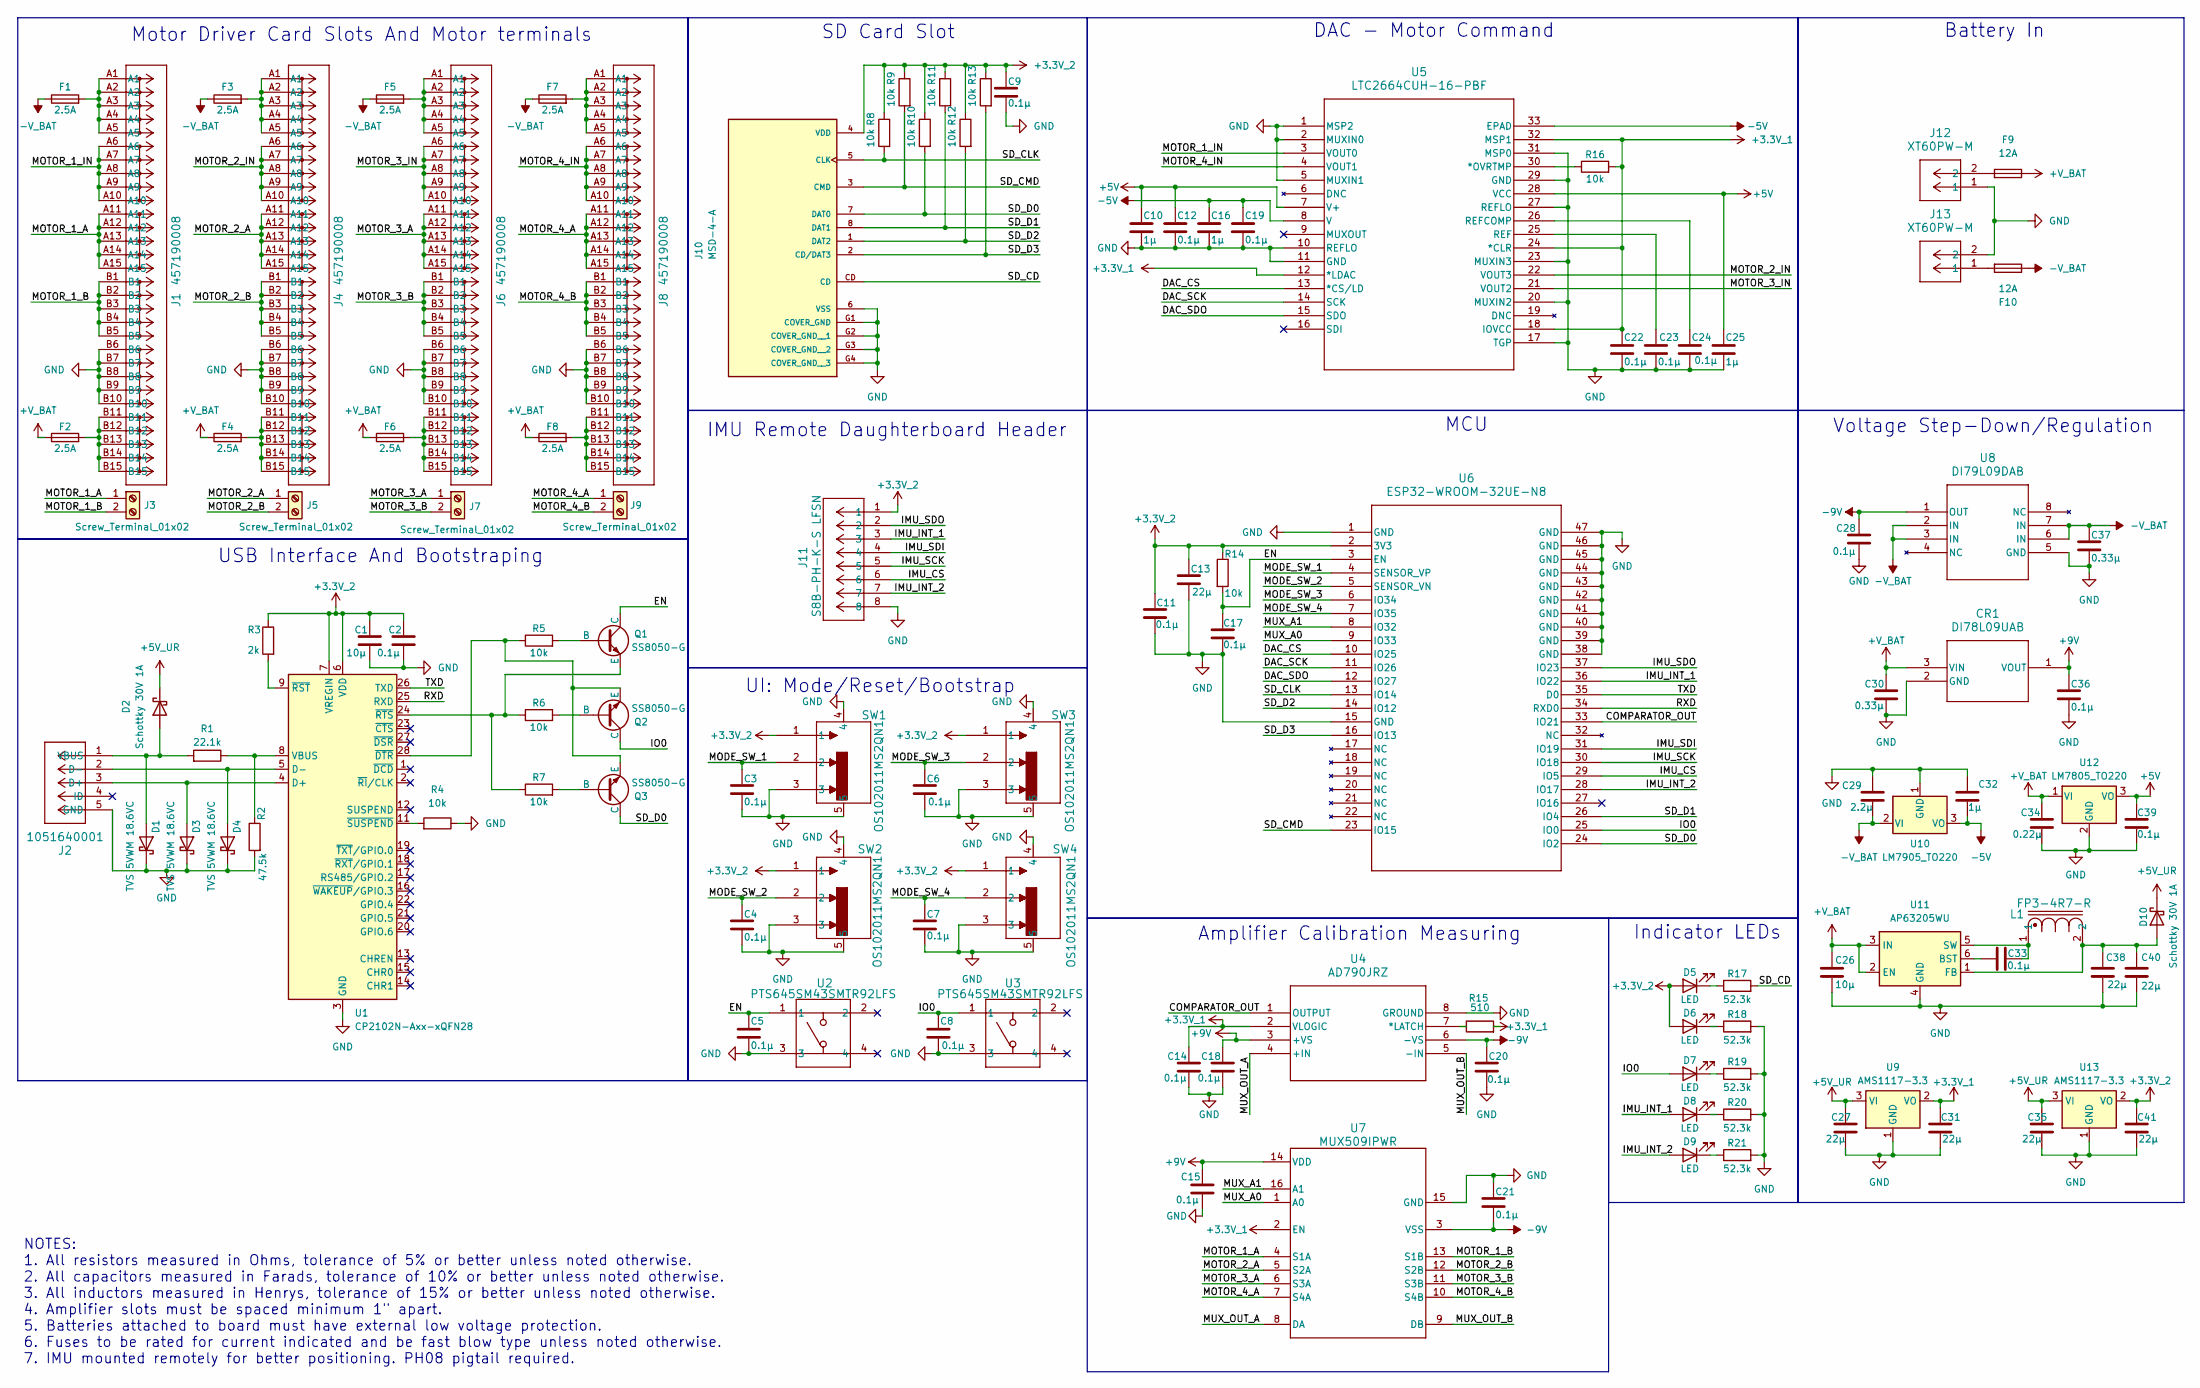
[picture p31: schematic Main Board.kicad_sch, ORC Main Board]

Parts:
C1, C26: 10μ; C_1206_3216Metric_Pad1.33x1.80mm_HandSolder
C2, C3, C4, C5, C6, C7, C8, C9, C11, C12, C14, C15, C17, C18, C19, C20, C21, C22, C23, C24, C28, C33, C36, C39: 0.1μ; C_1206_3216Metric_Pad1.33x1.80mm_HandSolder
C10, C16, C25, C32: 1μ; C_1206_3216Metric_Pad1.33x1.80mm_HandSolder
C13, C27, C31, C35, C38, C40, C41: 22μ; C_1206_3216Metric_Pad1.33x1.80mm_HandSolder
C29: 2.2μ; C_1206_3216Metric_Pad1.33x1.80mm_HandSolder
C30, C37: 0.33μ; C_1206_3216Metric_Pad1.33x1.80mm_HandSolder
C34: 0.22μ; C_1206_3216Metric_Pad1.33x1.80mm_HandSolder
CR1: DI78L09UAB; SOT-89_STM
D1, D3, D4: TVS 5VWM 18.6VC; D_0402_1005Metric_Pad0.77x0.64mm_HandSolder
D2, D10: Schottky 30V 1A; D_SOD-323_HandSoldering
D5, D6, D7, D8, D9: LED; LED_PLCC-2_3.4x3.0mm_KA
F1, F2, F3, F4, F5, F6, F7, F8: 2.5A; Fuse_1206_3216Metric_Pad1.42x1.75mm_HandSolder
F9, F10: 12A; Fuse_1206_3216Metric_Pad1.42x1.75mm_HandSolder
J1, J4, J6, J8: 457190008; CONN_SD-45719-001_3SEG_MOL
J2: 1051640001; CON00906_5_MOL
J3, J5, J7, J9: Screw_Terminal_01x02; TerminalBlock_TE_282834-2_1x02_P2.54mm_Horizontal
J10: MSD-4-A; CUI_MSD-4-A; PARTREV 1.0
J11: S8B-PH-K-S LFSN; CONN8_S8B-PH-K-S_JST
J12, J13: XT60PW-M; CONN_XT60PW-M_AMA
L1: FP3-4R7-R; FP3
Q1, Q2, Q3: SS8050-G; SOT-23-3
R1: 22.1k; R_1206_3216Metric_Pad1.30x1.75mm_HandSolder
R2: 47.5k; R_1206_3216Metric_Pad1.30x1.75mm_HandSolder
R3: 2k; R_1206_3216Metric_Pad1.30x1.75mm_HandSolder
R4, R5, R6, R7, R8, R9, R10, R11, R12, R13, R14, R16: 10k; R_1206_3216Metric_Pad1.30x1.75mm_HandSolder
R15: 510; R_1206_3216Metric_Pad1.30x1.75mm_HandSolder
R17, R18, R19, R20, R21: 52.3k; R_1206_3216Metric_Pad1.30x1.75mm_HandSolder
SW1, SW2, SW3, SW4: OS102011MS2QN1; SPDT_OS102011_CNK
U1: CP2102N-Axx-xQFN28; QFN-28-1EP_5x5mm_P0.5mm_EP3.35x3.35mm
U2, U3: PTS645SM43SMTR92LFS; SWITCH_43SMTR92LFS
U4: AD790JRZ; R_8_ADI
U5: LTC2664CUH-16-PBF; UH_32_ADI
U6: ESP32-WROOM-32UE-N8; ESP32-WROOM-32UE_EXP
U7: MUX509IPWR; PW0016A_N
U8: DI79L09DAB; SO8NB_STH
U9, U13: AMS1117-3.3; SOT-223-3_TabPin2
U10: LM7905_TO220; TO-220-3_Vertical
U11: AP63205WU; TSOT-23-6
U12: LM7805_TO220; TO-220-3_Vertical

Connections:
+3.3V_1: C14.1, C22.1, C31.1, R15.2, R16.2, U4.2 (VLOGIC), U5.12 (*LDAC), U5.18 (IOVCC), U5.24 (*CLR), U5.32 (MSP1), U7.2 (EN), U9.2 (VO)
+3.3V_2: C1.2, C2.1, C9.1, C11.1, C13.1, C41.1, D5.2 (A), D6.2 (A), J10.4 (VDD), J11.1, R3.1, R8.1, R9.1, R10.1, R11.1, R12.1, R13.1, R14.1, SW1.1, SW2.1, SW3.1, SW4.1, U1.6 (VDD), U1.7 (VREGIN), U6.2 (3V3), U13.2 (VO)
+5V: C10.1, C12.1, C25.1, C39.1, U5.7 (V+), U5.28 (VCC), U12.3 (VO)
+5V_UR: C27.1, C35.1, D2.1 (K), D10.1 (K), U9.3 (VI), U13.3 (VI)
+9V: C15.2, C18.1, C36.1, CR1.1 (VOUT), U4.3 (+VS), U7.14 (VDD)
+V_BAT: C26.1, C30.1, C34.1, CR1.3 (VIN), F2.1, F4.1, F6.1, F8.1, F9.1, U11.2 (EN), U11.3 (IN), U12.1 (VI)
-5V: C16.1, C19.1, C32.2, U5.8 (V), U5.33 (EPAD), U10.3 (VO)
-9V: C20.1, C21.2, C28.1, U4.6 (-VS), U7.3 (VSS), U8.1 (OUT)
-V_BAT: C29.2, C37.1, F1.1, F3.1, F5.1, F7.1, F10.1, U8.2 (IN), U8.3 (IN), U8.6 (IN), U8.7 (IN), U10.2 (VI)
/COMPARATOR_OUT: U4.1 (OUTPUT), U6.33 (IO21)
/DAC_CS: U5.13 (*CS/LD), U6.10 (IO25)
/DAC_SCK: U5.14 (SCK), U6.11 (IO26)
/DAC_SDO: U5.15 (SDO), U6.12 (IO27)
/EN: C5.1, C17.1, Q1.1 (C), R14.2, U2.1, U6.3 (EN)
/IMU_CS: J11.6, U6.29 (IO5)
/IMU_INT_1: D8.2 (A), J11.3, U6.36 (IO22)
/IMU_INT_2: D9.2 (A), J11.7, U6.28 (IO17)
/IMU_SCK: J11.5, U6.30 (IO18)
/IMU_SDI: J11.4, U6.31 (IO19)
/IMU_SDO: J11.2, U6.37 (IO23)
/IO0: C8.1, D7.2 (A), Q2.1 (C), U3.1, U6.25 (IO0)
/MODE_SW_1: C3.2, SW1.2, U6.4 (SENSOR_VP)
/MODE_SW_2: C4.2, SW2.2, U6.5 (SENSOR_VN)
/MODE_SW_3: C6.2, SW3.2, U6.6 (IO34)
/MODE_SW_4: C7.2, SW4.2, U6.7 (IO35)
/MOTOR_1_A: J1.A11, J1.A12, J1.A13, J1.A14, J1.A15, J3.1, U7.4 (S1A)
/MOTOR_1_B: J1.B1, J1.B2, J1.B3, J1.B4, J1.B5, J3.2, U7.13 (S1B)
/MOTOR_1_IN: J1.A6, J1.A7, J1.A8, J1.A9, J1.A10, U5.3 (VOUT0)
/MOTOR_2_A: J4.A11, J4.A12, J4.A13, J4.A14, J4.A15, J5.1, U7.5 (S2A)
/MOTOR_2_B: J4.B1, J4.B2, J4.B3, J4.B4, J4.B5, J5.2, U7.12 (S2B)
/MOTOR_2_IN: J4.A6, J4.A7, J4.A8, J4.A9, J4.A10, U5.22 (VOUT3)
/MOTOR_3_A: J6.A11, J6.A12, J6.A13, J6.A14, J6.A15, J7.1, U7.6 (S3A)
/MOTOR_3_B: J6.B1, J6.B2, J6.B3, J6.B4, J6.B5, J7.2, U7.11 (S3B)
/MOTOR_3_IN: J6.A6, J6.A7, J6.A8, J6.A9, J6.A10, U5.21 (VOUT2)
/MOTOR_4_A: J8.A11, J8.A12, J8.A13, J8.A14, J8.A15, J9.1, U7.7 (S4A)
/MOTOR_4_B: J8.B1, J8.B2, J8.B3, J8.B4, J8.B5, J9.2, U7.10 (S4B)
/MOTOR_4_IN: J8.A6, J8.A7, J8.A8, J8.A9, J8.A10, U5.4 (VOUT1)
/MUX_A0: U6.9 (IO33), U7.1 (A0)
/MUX_A1: U6.8 (IO32), U7.16 (A1)
/MUX_OUT_A: U4.4 (+IN), U7.8 (DA)
/MUX_OUT_B: U4.5 (-IN), U7.9 (DB)
/RXD: U1.25 (RXD), U6.34 (RXD0)
/SD_CD: J10.CD, R17.2
/SD_CLK: J10.5 (CLK), R8.2, U6.13 (IO14)
/SD_CMD: J10.3 (CMD), R9.2, U6.23 (IO15)
/SD_D0: J10.7 (DAT0), Q3.1 (C), R10.2, U6.24 (IO2)
/SD_D1: J10.8 (DAT1), R11.2, U6.26 (IO4)
/SD_D2: J10.1 (DAT2), R12.2, U6.14 (IO12)
/SD_D3: J10.2 (CD/DAT3), R13.2, U6.16 (IO13)
/TXD: U1.26 (TXD), U6.35 (D0)
GND: C1.1, C2.2, C3.1, C4.1, C5.2, C6.1, C7.1, C8.2, C9.2, C10.2, C11.2, C12.2, C13.2, C14.2, C15.1, C16.2, C17.2, C18.2, C19.2, C20.2, C21.1, C22.2, C23.2, C24.2, C25.2, C26.2, C27.2, C28.2, C29.1, C30.2, C31.2, C32.1, C34.2, C35.2, C36.2, C37.2, C38.2, C39.2, C40.2, C41.2, CR1.2 (GND), D1.1 (K), D3.1 (K), D4.1 (K), J1.B6, J1.B7, J1.B8, J1.B9, J1.B10, J2.5 (GND), J2.6, J2.7, J2.8, J2.9, J2.10, J2.11, J4.B6, J4.B7, J4.B8, J4.B9, J4.B10, J6.B6, J6.B7, J6.B8, J6.B9, J6.B10, J8.B6, J8.B7, J8.B8, J8.B9, J8.B10, J10.6 (VSS), J10.G1 (COVER_GND), J10.G2 (COVER_GND__1), J10.G3 (COVER_GND__2), J10.G4 (COVER_GND__3), J11.8, J12.1, J13.2, R2.2, R4.1, R18.2, R19.2, R20.2, R21.2, SW1.3, SW1.4, SW1.5, SW2.3, SW2.4, SW2.5, SW3.3, SW3.4, SW3.5, SW4.3, SW4.4, SW4.5, U1.3 (GND), U1.29 (GND), U2.3, U3.3, U4.8 (GROUND), U5.1 (MSP2), U5.2 (MUXIN0), U5.5 (MUXIN1), U5.10 (REFLO), U5.11 (GND), U5.17 (TGP), U5.20 (MUXIN2), U5.23 (MUXIN3), U5.27 (REFLO), U5.29 (GND), U5.31 (MSP0), U6.1 (GND), U6.15 (GND), U6.38 (GND), U6.39 (GND), U6.40 (GND), U6.41 (GND), U6.42 (GND), U6.43 (GND), U6.44 (GND), U6.45 (GND), U6.46 (GND), U6.47 (GND), U7.15 (GND), U8.5 (GND), U9.1 (GND), U10.1 (GND), U11.4 (GND), U12.2 (GND), U13.1 (GND)
unnamed: D1.2 (A), D2.2 (A), J2.1 (VBUS), R1.2
unnamed: D3.2 (A), J2.3 (D+), U1.4 (D+)
unnamed: D4.2 (A), J2.2 (D-), U1.5 (D-)
unnamed: D5.1 (K), R17.1
unnamed: D6.1 (K), R18.1
unnamed: D7.1 (K), R19.1
unnamed: D8.1 (K), R20.1
unnamed: D9.1 (K), R21.1
unnamed: C38.1, C40.1, D10.2 (A), L1.2, U11.1 (FB)
unnamed: F1.2, J1.A1, J1.A2, J1.A3, J1.A4, J1.A5
unnamed: F2.2, J1.B11, J1.B12, J1.B13, J1.B14, J1.B15
unnamed: F3.2, J4.A1, J4.A2, J4.A3, J4.A4, J4.A5
unnamed: F4.2, J4.B11, J4.B12, J4.B13, J4.B14, J4.B15
unnamed: F5.2, J6.A1, J6.A2, J6.A3, J6.A4, J6.A5
unnamed: F6.2, J6.B11, J6.B12, J6.B13, J6.B14, J6.B15
unnamed: F7.2, J8.A1, J8.A2, J8.A3, J8.A4, J8.A5
unnamed: F8.2, J8.B11, J8.B12, J8.B13, J8.B14, J8.B15
unnamed: F9.2, J12.2
unnamed: F10.2, J13.1
unnamed: Q1.2 (B), R5.2
unnamed: Q1.3 (E), R6.1, R7.1, U1.24 (~RTS)
unnamed: Q2.2 (B), R6.2
unnamed: Q2.3 (E), Q3.3 (E), R5.1, U1.28 (~DTR)
unnamed: Q3.2 (B), R7.2
unnamed: R1.1, R2.1, U1.8 (VBUS)
unnamed: R3.2, U1.9 (~RST)
unnamed: R4.2, U1.11 (~SUSPEND)
unnamed: R15.1, U4.7 (*LATCH)
unnamed: R16.1, U5.30 (*OVRTMP)
unnamed: C23.1, U5.25 (REF)
unnamed: C24.1, U5.26 (REFCOMP)
unnamed: C33.2, U11.6 (BST)
unnamed: C33.1, L1.1, U11.5 (SW)

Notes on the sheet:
NOTES: 1. All resistors measured in Ohms, tolerance of 5% or better unless noted otherwise. 2. All capacitors measured in Farads, tolerance of 10% or better unless noted otherwise. 3. All inductors measured in Henrys, tolerance of 15% or better unless noted otherwise. 4. Amplifier slots must be spa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
UI: Mode/Reset/Bootstrap
Motor Driver Card Slots And Motor terminals
Voltage Step-Down/Regulation
SD Card Slot
IMU Remote Daughterboard Header
USB Interface And Bootstraping
MCU
DAC - Motor Command
Battery In
Indicator LEDs
Amplifier Calibration Measuring

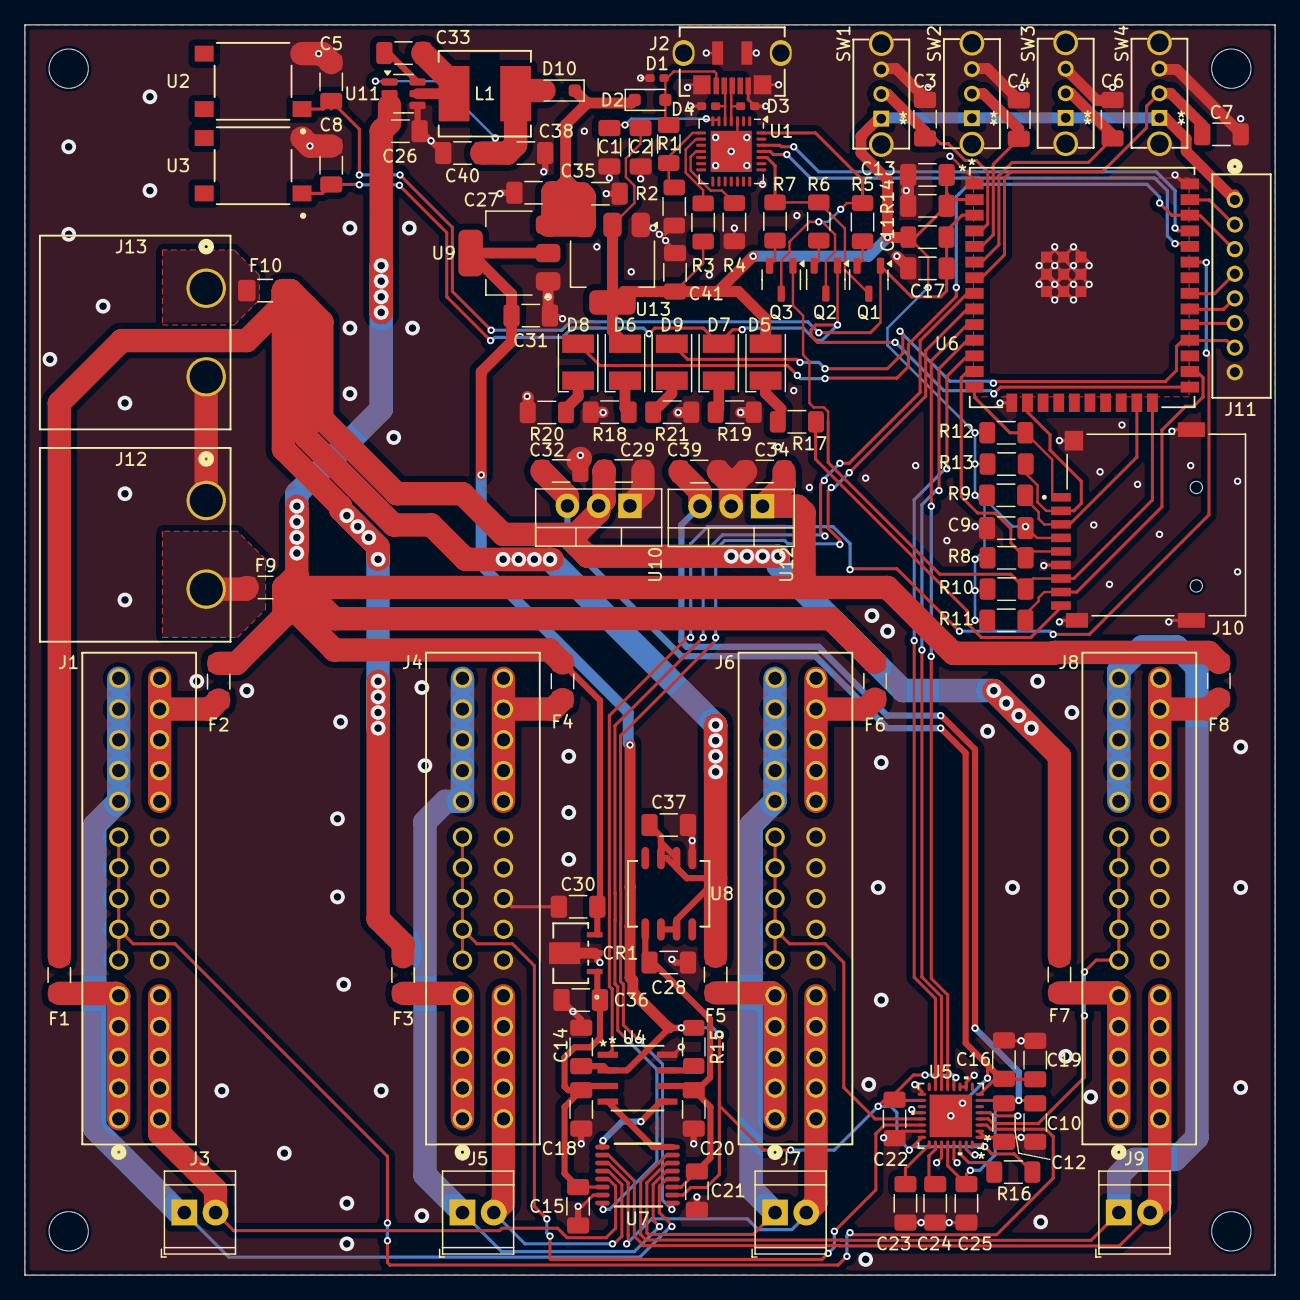
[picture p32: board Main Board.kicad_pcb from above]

Board: 2 copper layers, 101.6 x 101.6 mm, 117 parts (0 on the bottom side), 84 nets.

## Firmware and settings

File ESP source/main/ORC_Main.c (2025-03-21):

/**
  ******************************************************************************
  * @file    ORC_Main.c
  * @author  Corbin Roennebeck, WSU
  * @brief   Controls actuators and logs data for ORC project as defined by 
  *             "Theory of Operation", below.
  ******************************************************************************
  */

  /**
   *    Theory of Operation:
   *        The motions of 4 actuators between the vehicle frame and axle,
   *        located both front and rear on both the driver and passenger side,
   *        is controlled by 3 PID controllers. These controlers use measured
   *        vehicle dynamics - vertical acceleration (less gravity), pitch, and 
   *        roll - to define actuator motion that cancels out the aforementioned 
   *        vehicle dynamics. The measured vehicle dynamics are also capable of
   *        being logged to the onboard SD card. These vehicle dynamics are
   *        measured by the attached IMU, filtered onboard the IMU, and processed
   *        by the AHRS Fusion library to provide accurate, realtime information.
   *
   *    More detailed information can be found in the "ORC Documentation.pdf" file
   */

#include <stdio.h>
#include <stdlib.h>
#include <string.h>
#include <sys/unistd.h>
#include <sys/stat.h>
#include "esp_vfs_fat.h"
#include "sdmmc_cmd.h"
#include "driver/sdmmc_host.h"
#include "freertos/FreeRTOS.h"
#include "freertos/task.h"
#include "driver/spi_master.h"
#include "driver/spi_common.h"
#include "driver/gpio.h"
#include "sdkconfig.h"
#include "esp_log.h"
#include "esp_timer.h"
#include "esp_intr_types.h"
#include "esp_random.h"

#include "Fusion.h"
#include "LTC2664_reg.h"
#include "ism330dhcx_reg.h"
#include "Transform.h"
#include "PID.h"

#include "ORC_CONFIG.h"

//spi functions for devices, platform delay for advanced IMU functions
static int32_t DAC_write(void *handle, ltc2664_DACS_t dac, uint8_t command, const uint16_t *data);
static int32_t IMU_write(void *handle, uint8_t reg, const uint8_t *bufp, uint16_t len);
static int32_t IMU_read(void *handle, uint8_t reg, uint8_t *bufp, uint16_t len);
static void platform_delay(uint32_t ms);

//initialization and configuration functions
static esp_err_t init_spi_IMU();
static esp_err_t init_spi_DAC();
static void init_pid_controllers(void);
static esp_err_t config_IMU(void);
static esp_err_t config_DAC(void);

//data structure to pass data from IMU Sampling to SD writing
typedef struct
{
    float_t acceleration_z;
    float_t pitch;
    float_t roll;

}log_data_t;
static QueueHandle_t log_data_queue = NULL;

//spi handle and device reference for IMU
static stmdev_ctx_t ISM330DHCX_dev_ctx;
static spi_device_handle_t IMU_spi;

//spi handle and device reference for DAC
static ltcdev_ctx_t LTC2664_dev_ctx;
static spi_device_handle_t DAC_spi;

//reference for IMU_sample_task
static TaskHandle_t IMU_TASK;

//time between IMU samples, reported by IMU
static float_t float_time = 0;

//PID Contoller Handles
static PIDController_t accel_z_controller={};
static PIDController_t pitch_controller={};
static PIDController_t roll_controller={};

//Boot Config booleans
static bool en_logging = false;
static bool en_actuators = false;


/**
 * @brief Capture interupt from IMU and tell the IMU_sample_task there's data avalible
 */
static void IRAM_ATTR imu_isr_handler(void* arg){
    BaseType_t higherPriorityTask = pdTRUE;
    vTaskNotifyGiveFromISR(IMU_TASK,&higherPriorityTask);
}

/**
 * @brief Initialize the IMU, it's interupts, and the fusion library, then perform continuous sampling.
 */
static void IMU_sample_task(void* arg)
{
    esp_err_t err;
    //buffers for IMU data to be placed in
    int16_t data_raw_acceleration[3];
    int16_t data_raw_angular_rate[3];
    //data frame for log data to be queued
    log_data_t df;
    //PID outputs
    float_t acceleration_z_float = 0;
    float_t pitch_float;
    float_t roll_float;
    //Fusion handle, outputs, and inputs
    FusionAhrs ahrs;
    FusionEuler euler;
    FusionVector linear;
    FusionVector gyroscope = {{0,0,0}};
    FusionVector accelerometer = {{0,0,0}};
    //Transformed PID outputs to be sent to DAC
    uint16_t actuator1, actuator2, actuator3, actuator4;

    const char TAG[] = "IMU Sampling Task";

    /* Initialize and configure IMU*/
    err = init_spi_IMU();
    ESP_ERROR_CHECK(err);
    err = config_IMU();
    ESP_ERROR_CHECK(err);        
    
    //set up fusion algorithm, use standard values as defined in Fusion Library
    FusionAhrsInitialise(&ahrs);
    FusionAhrsSettings * const ahrs_settings = malloc(sizeof(FusionAhrsSettings));
    ahrs_settings->accelerationRejection =  10; //degrees
    ahrs_settings->gyroscopeRange =         500;//dps
    ahrs_settings->gain =                   0.5f; //influence of gyroscope
    ahrs_settings->convention =             FusionConventionEnu; //earth axes convention (consistent with ISM330DHCX)
    ahrs_settings->recoveryTriggerPeriod =  5.0/float_time; //approx 5 second recovery trigger period
    FusionAhrsSetSettings(&ahrs, ahrs_settings);

    ESP_LOGI(TAG, "AHRS Initialized");

    /* Initialize PID Controllers */
    init_pid_controllers();

    /* Initialize  and configure DAC */
    err = init_spi_DAC();
    ESP_ERROR_CHECK(err);
    err = config_DAC();
    ESP_ERROR_CHECK(err);

    /* Initialize Transform Matrix Distances */
    err = set_distances(FA_COG,RA_COG,DA_COG,PA_COG);
    ESP_ERROR_CHECK(err);
    ESP_LOGI(TAG,"Distaces set\nF-%.3f\nR-%.3f\nD-%.3f\nP-%.3f", FA_COG, RA_COG, DA_COG, PA_COG);
    
    /* Calibrate the rest angle and acceleration for the vehicle */
    /*-----------------------------------------------------------*/
    /* Read a register from the IMU to kick off interupt sampling */
    ism330dhcx_angular_rate_raw_get(&ISM330DHCX_dev_ctx, data_raw_angular_rate);
    ism330dhcx_acceleration_raw_get(&ISM330DHCX_dev_ctx, data_raw_acceleration);

    /* While fusion isn't stable, keep reading the IMU.*/
    FusionAhrsFlags fusionFlags = FusionAhrsGetFlags(&ahrs);
    while(fusionFlags.initialising || fusionFlags.angularRateRecovery){
        ulTaskNotifyTake(pdFALSE,portMAX_DELAY);
        //when IMU_PIN_INT1 rising edge

        //read accel/gyro
        memset(data_raw_acceleration, 0x00, 3 * sizeof(int16_t));
        ism330dhcx_acceleration_raw_get(&ISM330DHCX_dev_ctx, data_raw_acceleration);
        ism330dhcx_angular_rate_raw_get(&ISM330DHCX_dev_ctx, data_raw_angular_rate);
        
        //convert to dps for use in Fusion
        //uses full scale of 500dps for int to float conversion
        //reuse old data if peak detected
        for(int i=0; i<3; i++){
            if(data_raw_angular_rate[i] < IMU_GY_PEAK_REJ && data_raw_angular_rate[i] > -IMU_GY_PEAK_REJ){
                gyroscope.array[i] = (float_t)data_raw_angular_rate[i] * 0.0175f;
            }
        }

        //convert to g for use in Fusion 
        //uses full scale of 4 g for int to float conversion
        //reuse old data if peak detected
        for(int i=0; i<3; i++){
            if(data_raw_angular_rate[i] < IMU_XL_PEAK_REJ && data_raw_angular_rate[i] > -IMU_XL_PEAK_REJ){
                accelerometer.array[i] = (float_t)data_raw_acceleration[i] * 0.000122f;
            }
        }
        //update Fusion
        FusionAhrsUpdateNoMagnetometer(&ahrs, gyroscope, accelerometer, float_time);
        //refresh flags
        fusionFlags = FusionAhrsGetFlags(&ahrs);
    }
    //once data is stable, set zeros to use for PID setpoint
    euler = FusionQuaternionToEuler(FusionAhrsGetQuaternion(&ahrs));
    float_t acceleration_zero = 0;  //set to zero, as noise crushing performed on xl data later would remove this offset
    float_t pitch_zero = euler.angle.pitch;
    float_t roll_zero = euler.angle.roll;

    ESP_LOGI(TAG, "Acceleration zero point: %.3f", acceleration_zero);
    ESP_LOGI(TAG, "Pitch zero point: %.3f", pitch_zero);
    ESP_LOGI(TAG, "Roll zero point: %.3f", roll_zero);

    //delay to ensure SD card is rady
    vTaskDelay(100);

    /* Turn on Status LEDs */+
    gpio_set_level(STATUS_LED2, 1);
    gpio_set_level(STATUS_LED1, 1);

    /* Read a register from the IMU to kick off interupt sampling again, log collected data, control actuators as needed */
    /*-------------------------------------------------------------------------------------------------------------------*/
    ism330dhcx_angular_rate_raw_get(&ISM330DHCX_dev_ctx, data_raw_angular_rate);
    ism330dhcx_acceleration_raw_get(&ISM330DHCX_dev_ctx, data_raw_acceleration);
    ESP_LOGI(TAG,"Sampling started");

    while(1){
        ulTaskNotifyTake(pdFALSE,portMAX_DELAY);
        //when IMU_PIN_INT1 rising edge

        //read accel/gyro
        memset(data_raw_acceleration, 0x00, 3 * sizeof(int16_t));
        ism330dhcx_acceleration_raw_get(&ISM330DHCX_dev_ctx, data_raw_acceleration);
        ism330dhcx_angular_rate_raw_get(&ISM330DHCX_dev_ctx, data_raw_angular_rate);
        
        //convert to dps for use in Fusion
        //uses full scale of 500dps for int to float conversion
        //reuse old data if peak detected
        for(int i=0; i<3; i++){
            if(data_raw_angular_rate[i] < IMU_GY_PEAK_REJ && data_raw_angular_rate[i] > -IMU_GY_PEAK_REJ){
                gyroscope.array[i] = (float_t)data_raw_angular_rate[i] * 0.0175f;
            }
        }

        //convert to g for use in Fusion 
        //uses full scale of 4 g for int to float conversion
        //reuse old data if peak detected
        for(int i=0; i<3; i++){
            if(data_raw_angular_rate[i] < IMU_XL_PEAK_REJ && data_raw_angular_rate[i] > -IMU_XL_PEAK_REJ){
                accelerometer.array[i] = (float_t)data_raw_acceleration[i] * 0.000122f;
            }
        }
        //update Fusion, and get the resulting values
        FusionAhrsUpdateNoMagnetometer(&ahrs, gyroscope, accelerometer, float_time);
        euler = FusionQuaternionToEuler(FusionAhrsGetQuaternion(&ahrs)); //angles
        linear = FusionAhrsGetLinearAcceleration(&ahrs); //acceleration less gravity

        //send data to be logged
        df.acceleration_z = linear.axis.z;
        df.pitch = euler.angle.pitch;
        df.roll = euler.angle.roll;
        xQueueSendToBack(log_data_queue,&df,0);

        //crush acceleration data to 0 if below noise floor, crushing is based on absolute value of input data
        float_t conditioned_acceleration_z = 0;
        if (linear.axis.z > IMU_NOISE_FLOOR){
            conditioned_acceleration_z = linear.axis.z - IMU_NOISE_FLOOR;
        }
        else if (linear.axis.z < -IMU_NOISE_FLOOR){
            conditioned_acceleration_z = linear.axis.z + IMU_NOISE_FLOOR;
        }

        if(en_actuators == true){// below sections not needed if actuators disabled
            //pid updates
            acceleration_z_float = PIDController_Update(&accel_z_controller, &acceleration_zero, &conditioned_acceleration_z);
            pitch_float = PIDController_Update(&pitch_controller, &pitch_zero, &euler.angle.pitch);
            roll_float = PIDController_Update(&roll_controller, &roll_zero, &euler.angle.roll);

            //transform
            transform(&actuator1,&actuator2,&actuator3,&actuator4,&acceleration_z_float,&pitch_float,&roll_float);

            //write to dac refer to page 73 of Notebook or design document for mapping, dependent on physical wiring
            ltc2664_write_and_update_1_dac(&LTC2664_dev_ctx, LTC2664_DAC_1, &actuator1);
            ltc2664_write_and_update_1_dac(&LTC2664_dev_ctx, LTC2664_DAC_2, &actuator2);
            ltc2664_write_and_update_1_dac(&LTC2664_dev_ctx, LTC2664_DAC_0, &actuator3);
            ltc2664_write_and_update_1_dac(&LTC2664_dev_ctx, LTC2664_DAC_3, &actuator4);

        }        
    }
}

/**
    @brief Initialize the ISM330DHCX_device's SPI bus
*/
esp_err_t init_spi_IMU(void){
    esp_err_t ret;

    static const char init_spi_TAG[] = "IMU";
    ESP_LOGI(init_spi_TAG, "Initializing bus SPI%d...", IMU_HOST + 1);

    spi_bus_config_t *buscfg = malloc(sizeof(spi_bus_config_t)); //save this config in the heap
    memset(buscfg,0xFF,sizeof(spi_bus_config_t)); //disable extra config pins
    buscfg->miso_io_num = IMU_PIN_NUM_MISO;
    buscfg->mosi_io_num = IMU_PIN_NUM_MOSI;
    buscfg->sclk_io_num = IMU_PIN_NUM_CLK; 
    buscfg->quadwp_io_num = -1,
    buscfg->quadhd_io_num = -1,
    buscfg->max_transfer_sz = 8; //limit transfer sz to 8 bytes
    buscfg->flags = 0;
    buscfg->data_io_default_level = 0;
    buscfg->intr_flags = 0;
    buscfg->isr_cpu_id = ESP_INTR_CPU_AFFINITY_AUTO;

    ret = spi_bus_initialize(IMU_HOST, buscfg, SPI_DMA_DISABLED); //initialize the bus using the controller defined in the preamble
    
    if(ret != ESP_OK){ // if we have an error
        return (ret); //cancel any further operation and return
    }
    //else continue setup

    ESP_LOGI(init_spi_TAG, "Init Success. Adding device...");
    
    spi_device_interface_config_t *devcfg = malloc(sizeof(spi_device_interface_config_t));
    memset(devcfg,0x00,sizeof(spi_device_interface_config_t));//zero out memory space
    devcfg->command_bits =      1;//one command bit (R/W)
    devcfg->address_bits =      7;//seven address bit (register address)
    devcfg->mode=               3;//Clock high in idle, read on rising edge
    devcfg->clock_source =      SPI_CLK_SRC_DEFAULT;
    devcfg->duty_cycle_pos =    128;//50%/50% duty cycle
    devcfg->cs_ena_pretrans =   0;//CS timed with clock
    devcfg->cs_ena_posttrans =  0;
    devcfg->clock_speed_hz=     9*1000*1000; //10Mhz
    devcfg->input_delay_ns =    0;
    devcfg->spics_io_num=       IMU_PIN_NUM_CS;
    devcfg->flags =             SPI_DEVICE_NO_DUMMY; //disable high freq(>100MHZ) workaround
    devcfg->queue_size=         7;  //queue 7 transactions at most
    devcfg->pre_cb =            NULL; //No callbacks
    devcfg->post_cb =           NULL;

    ret = spi_bus_add_device(IMU_HOST, devcfg, &IMU_spi);

    if(ret != ESP_OK){ // if we have an error
        return (ret); //cancel any further operation and return
    }

    //now the IMU device can have it's associated functions and handle defined
    ISM330DHCX_dev_ctx.write_reg = IMU_write;
    ISM330DHCX_dev_ctx.read_reg = IMU_read;
    ISM330DHCX_dev_ctx.mdelay = platform_delay;
    ISM330DHCX_dev_ctx.handle = IMU_spi;

    ESP_LOGI(init_spi_TAG, "Device driver ready for use");

    return(ret);

}
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
void app_main(void){
    static const char TAG[] = "Main";
    esp_err_t err;

/* GPIO CONFIGURATION SECTION */
    /* Configure Interupt Pin For IMU */
    gpio_config_t io_conf = {};
    io_conf.intr_type = GPIO_INTR_POSEDGE;
    io_conf.pin_bit_mask = GPIO_INT_PIN_SEL;
    io_conf.mode = GPIO_MODE_INPUT;
    io_conf.pull_up_en = 0;
    io_conf.pull_down_en = 0;
    gpio_config(&io_conf);
    /* Configure IMU_MISO Pin */
    io_conf.intr_type = GPIO_INTR_DISABLE;
    io_conf.pin_bit_mask = GPIO_MISO_PIN;
    io_conf.mode = GPIO_MODE_INPUT;
    io_conf.pull_up_en = 1;
    io_conf.pull_down_en = 0;
    gpio_config(&io_conf);
    /* Configure Mux Address Pins */
    io_conf.intr_type = GPIO_INTR_DISABLE;
    io_conf.pin_bit_mask = GPIO_MUX_PINS;
    io_conf.mode = GPIO_MODE_OUTPUT;
    io_conf.pull_down_en = 0;
    io_conf.pull_up_en = 0;
    gpio_config(&io_conf);
    /* Configure Comparator Signal Pin */
    io_conf.intr_type = GPIO_INTR_DISABLE;
    io_conf.pin_bit_mask = GPIO_COMP_PINS;
    io_conf.mode = GPIO_MODE_INPUT;
    io_conf.pull_down_en = 0;
    io_conf.pull_up_en = 0;
    gpio_config(&io_conf);
    /* Configure Status LED Pin */
    io_conf.intr_type = GPIO_INTR_DISABLE;
    io_conf.pin_bit_mask = GPIO_STATUS_PINS;
    io_conf.mode = GPIO_MODE_OUTPUT;
    io_conf.pull_down_en = 0;
    io_conf.pull_up_en = 0;
    gpio_config(&io_conf);
    /* Configure Mode Switches Pin */
    io_conf.intr_type = GPIO_INTR_DISABLE;
    io_conf.pin_bit_mask = GPIO_MODE_SWS_HIGH;
    io_conf.mode = GPIO_MODE_INPUT;
    io_conf.pull_down_en = 0;
    io_conf.pull_up_en = 0;
    gpio_config(&io_conf);
    io_conf.intr_type = GPIO_INTR_DISABLE;
    io_conf.pin_bit_mask = GPIO_MODE_SWS_LOW;
    io_conf.mode = GPIO_MODE_INPUT;
    io_conf.pull_down_en = 1;
    io_conf.pull_up_en = 0;
    gpio_config(&io_conf);
    /* Read boot config switches, write global bools */
    if(gpio_get_level(MODE_SW_EN_LOGGING) == 1){
        ESP_LOGI(TAG,"Logging Enabled");
        en_logging = true; 
    }
    if(gpio_get_level(MODE_SW_EN_ACTUATOR) == 1){ 
        ESP_LOGI(TAG,"Actuators Enabled");
        en_actuators = true;
    }
    /* Turn off Status LED, not ready yet */
    gpio_set_level(STATUS_LED2, 0);    
    gpio_set_level(STATUS_LED1, 0);

    /* Create Queue for transfering data to SD card function */
    log_data_queue = xQueueCreate(7000, sizeof(log_data_t));

    /* Start tasks for IMU sampling*/
    ESP_LOGI(TAG, "Starting IMU Task");
    xTaskCreatePinnedToCore(IMU_sample_task, "IMU_sample_task", 4096, NULL, 9, &IMU_TASK, APP_CPU_NUM);

    /* Set up ISR */
    ESP_LOGI(TAG, "Installing ISR");
    err = gpio_install_isr_service(0);
    ESP_ERROR_CHECK(err);
    err = gpio_isr_handler_add(IMU_PIN_INT1, imu_isr_handler, (void*) IMU_PIN_INT1);
    ESP_ERROR_CHECK(err);   

    if(en_logging == true){//do not continue if logging is not enabled
        /* Initialize SD Card*/
        esp_vfs_fat_sdmmc_mount_config_t mount_config = {
            .max_files = 5,
            .allocation_unit_size = 16 * 1024
        };
        sdmmc_card_t *card;
        const char mount_point[] = MOUNT_POINT;
        ESP_LOGI(TAG, "Initializing SD card");

        ESP_LOGI(TAG, "Using SDMMC peripheral");

        //Increase the speed here as much as possible
        sdmmc_host_t host = SDMMC_HOST_DEFAULT();
        host.max_freq_khz = 45000;

        sdmmc_slot_config_t slot_config = SDMMC_SLOT_CONFIG_DEFAULT();
        slot_config.width = 4;
        slot_config.clk = SD_PIN_CLK;
        slot_config.cmd = SD_PIN_CMD;
        slot_config.d0 = SD_PIN_D0;
        slot_config.d1 = SD_PIN_D1;
        slot_config.d2 = SD_PIN_D2;
        slot_config.d3 = SD_PIN_D3;
        slot_config.flags |= SDMMC_SLOT_FLAG_INTERNAL_PULLUP;

        ESP_LOGI(TAG, "Mounting filesystem");
        err = esp_vfs_fat_sdmmc_mount(mount_point, &host, &slot_config, &mount_config, &card);

        if (err != ESP_OK) {
            if (err == ESP_FAIL) {
                ESP_LOGE(TAG, "Failed to mount filesystem.");
            } else {
                ESP_LOGE(TAG, "Failed to initialize the card (%s).", esp_err_to_name(err));
            }
            return;
        }
        ESP_LOGI(TAG, "Filesystem mounted");

        sdmmc_card_print_info(stdout, card);

        char temp_string[33];//char array to have each line of log temporarily printed to. allows formating to be applied
        char *cache = malloc(CACHE_SIZE);   //cache allocation to store blocks of data to write to SD card, helps maintain write speed as less wear leveling takes place

        char *file_name = MOUNT_POINT"/ORClog.csv";//specify the file to be written to
        
        //attempt to open file
        ESP_LOGI(TAG, "Opening file %s", file_name);
        FILE *f = fopen(file_name, "a");
        if (f == NULL) {
            ESP_LOGE(TAG, "Failed to open file for writing");
            return;
        }

        /* Log title block*/
        int written_length = snprintf(temp_string, 32, "Log #: %li\n", esp_random() % 10000);//random 4 digit log number, differentiates multiple test in one file
        memcpy(cache, temp_string, written_length);
        uint32_t lines = written_length;
        if(en_actuators){
            written_length = snprintf(temp_string, 32, "Actuators enabled\n");
        }
        else{
            written_length = snprintf(temp_string, 32, "Actuators disabled\n");
        }
        memcpy(cache + (lines), temp_string, written_length);
        lines += written_length;
        while(float_time == 0){
            vTaskDelay(100);
        }
        written_length = snprintf(temp_string, 32, "Interval:%f\n", float_time);
        memcpy(cache + (lines), temp_string, written_length);
        lines += written_length;
        written_length = snprintf(temp_string, 32, "Acceleration, Pitch, Roll\n");
        memcpy(cache + (lines), temp_string, written_length);
        lines += written_length;

        ESP_LOGI(TAG, "Begin Normal Operation");
        log_data_t log_data;
        while(gpio_get_level(MODE_SW_START_LOG) == 0){
            vTaskDelay(100);
        }
        //clear the queue right before we start saving data.
        xQueueReset(log_data_queue);
        while(1){
            if(xQueueReceive(log_data_queue,&log_data, 0)){
                //when a new sample comes in, write it to the cache
                written_length = snprintf(temp_string, 32, "%.4f, %.4f, %.4f\n", log_data.acceleration_z, log_data.pitch, log_data.roll);
                memcpy(cache + (lines), temp_string, written_length);
                lines += written_length;
                //if the cahce is nearly full, write it to the sd card
                if(lines >= CACHE_SIZE-64){ //lose as much as 1 second of data by saving approx. every second.
                    cache[lines] = '\0';
                    lines = 0;
                    fprintf(f, cache);
                    //close file, saves data written
                    fclose(f);
                    if(gpio_get_level(MODE_SW_START_LOG) == 0){//if log not paused
                        //wait till next log should begin
                        while(gpio_get_level(MODE_SW_START_LOG) == 0){
                            vTaskDelay(100);
                        }
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

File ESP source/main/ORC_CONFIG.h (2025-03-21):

/**
  ******************************************************************************
  * @file    ORC_CONFIG.h
  * @author  Corbin Roennebeck, WSU
  * @brief   Constants and Configurations for ORC_Main
  ******************************************************************************
  */

#ifndef ORC_CONFIG_H
#define ORC_CONFIG_H

/* Calibration System IO / pin masks */
#define MUX_PIN_A0      33
#define MUX_PIN_A1      32
#define COMPARATOR_PIN  21
#define GPIO_MUX_PINS   ((1ULL<<MUX_PIN_A0) | (1ULL<<MUX_PIN_A1))
#define GPIO_COMP_PINS  (1ULL<<COMPARATOR_PIN)
/* SD Card IO / constants */
#define CACHE_SIZE      8192*8   //bytes
#define MOUNT_POINT     "/sdcard"
#define SD_PIN_D3       13
#define SD_PIN_D2       12
#define SD_PIN_CLK      14
#define SD_PIN_CMD      15
#define SD_PIN_D0       2
#define SD_PIN_D1       4
/* IMU IO / pin masks / spi controller */
#define IMU_HOST            VSPI_HOST
#define IMU_BOOT_TIME       10 //ms
#define IMU_PIN_NUM_MISO    23
#define IMU_PIN_NUM_MOSI    19
#define IMU_PIN_NUM_CLK     18
#define IMU_PIN_NUM_CS      5
#define IMU_PIN_INT1        22
#define GPIO_INT_PIN_SEL    (1ULL<<IMU_PIN_INT1)
#define GPIO_MISO_PIN       (1ULL<<IMU_PIN_NUM_MISO)
/* DAC IO / spi controller */
#define DAC_HOST            HSPI_HOST
#define DAC_PIN_NUM_MISO    -1
#define DAC_PIN_NUM_MOSI    27
#define DAC_PIN_NUM_CLK     26
#define DAC_PIN_NUM_CS      25
/* UI IO / pin masks */
#define STATUS_LED1         17
#define STATUS_LED2         0
#define GPIO_STATUS_PINS    ((1ULL<<STATUS_LED2) | (1ULL<<STATUS_LED1))
#define MODE_SW_EN_LOGGING  34  //enable logging
#define MODE_SW_EN_ACTUATOR 35  //enable actuators
#define MODE_SW_START_LOG   36  //start and stop log via this switch
#define MODE_SW_APPEND_LOG  39  //choose to start new log (same file) or append to previous after pause
#define GPIO_MODE_SWS_HIGH  ((1ULL<<MODE_SW_EN_ACTUATOR) | (1ULL<<MODE_SW_EN_LOGGING) | (1ULL<<MODE_SW_APPEND_LOG))
#define GPIO_MODE_SWS_LOW   (1ULL<<MODE_SW_START_LOG)
/* nonlinear filter constants */
#define IMU_XL_PEAK_REJ     30738 //eq to 3.75g in int16 output data format, reject xl values above this limit (below for negative)
#define IMU_GY_PEAK_REJ     28572 //eq to 500dps in int16 output data format, reject gy values above this limit (below for negative)
#define IMU_NOISE_FLOOR     0.003f //crush all xl data +- this value to zero
/* distances */
#define FA_COG      0.011    //distance to front axle linkages (in meters) from COG
#define RA_COG      0.018    //distance to rear axle linkages (in meters) from COG
#define DA_COG      0.008    //distance to drive side linkages (in meters) from COG
#define PA_COG      0.008    //distance to passenger side linkages (in meters) from COG
/* PID constants */
#define Z_XL_KP     -30000.0f
#define Z_XL_KI     -0.0f    //integral can be unstable, without providing much to response, possible value: -8000
#define Z_XL_KD     -1800.0f
#define PITCH_KP    -70.0f
#define PITCH_KI    -1.50f
#define PITCH_KD    -1.0f
#define ROLL_KP     -50.0f
#define ROLL_KI     -1.50f
#define ROLL_KD     -1.0f


#endif //ORC_CONFIG_H

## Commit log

2025-02-11 Make IMU work from interupt (broken)
2025-02-12 Added PID library. IMU working, requires debug still
2025-02-14 IMU output chained to DAC, Need level based interrupts implemented.
2025-02-18 Added Calibration to the DACs. Will get within 3LSB of a true "zero" assuming minimal variance from theroretical zero. Adjustment direction may need modified.
2025-03-06 Bug fixes with DAC output, Renaming for clarification, Add startup pitch/roll/acceleration calibration, Add status LED output, Add Mode Switch configuration, better format for logging
    [ORC_Main.c]
2025-03-08 readability fixes, other consolidations
    [ORC_Main.c]
2025-03-11 Sampling rate issues fixed. Able to do 3khz. now tuning PIDs
    [ORC_Main.c]
2025-03-14 IMU filtering implemented. 3D models, schematics now tracked. Code commented in detail.
    [8mm M3 spacer-Body.stl, 8mm M3 spacer-BodySketch001.stl, 8mm M3 spacer.FCStd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]
2025-03-21 PIDs tuned. Start switch wired to RC reciever. Battery inputs routed through relays. Camber test data collected and processed. DAC output code better clamped. Calibration bypassed, MUX is dead.
    [Arm-Body.stl, Arm.FCStd, Tight turn slide wheel-Body.stl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]
2025-03-21 Vibration test added, both high and low speed
    [ORCLOG_vibration_HS.CSV]
2025-03-22 Graphs changed to show only single run. Better for printing and easy understanding. T-test added. All current data re-ran
    [ORCLOG_vibration_HS.CSV]
